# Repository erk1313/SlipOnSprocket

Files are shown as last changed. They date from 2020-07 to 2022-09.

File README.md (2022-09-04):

### Slip-On Sprocket for the Early-Rider 16" Belt-Driven Bicycle

The Early Rider Belter/Seeker 16 comes with a tall gear ratio that's tough for hilly areas or timid riders.  The easiest thing is to buy a bike with a chain with a replaceable sprocket, but what's the fun in that?! This project is for a rear sprocket that slips over the existing 22t sprocket.

Here's how the gain ratio of popular 16" bikes stack up.  Lower ratios make it easier to climb hills, while higher ratios limit top speed on straight-aways.  The Early Rider comes with a 46t front chainring and a 22t rear sprocket, making it the highest gain ratio on this list

### Gain Ratios of 16" bikes*
| Bike | Gain Ratio | Gear Ratio  | Crank Length  | TIRE OD | Notes|
|---|---|---|---|---|---|
|Early Rider (Seeker)|4.05 |46/22t **STOCK**|105mm |407mm**  ||
|Spawn Yoji |3.97 |24/12t |102mm |405mm* | |
|Prevalo Alpha |3.80 |25t/14t |**95mm** |403mm* |Gain Ratio listed on [Prevalo](https://prevelobikes.com/products/alpha-two) |
|Early Rider (Hellion)|3.70 |30/15t |110mm |407mm**  || 
|Woom 3 |3.54 |25/15t | **95mm** |403mm* ||
|Islabike Cnoc |3.52 |25/14t |102mm |401mm* ||
|Priority Start |3.38 |? |? |? |Gain Ratio listed on [Priority Start](https://www.prioritybicycles.com/products/startfw2) |
|Commencal Ramones |3.12 |28/16t |114mm |407mm**  ||
|Cleary Hedgehog |3.09 |25/16t |102mm |404mm* |Flip-flop hub with 14t would result in Gain Ration of 3.54 (like a Woom 3)|
|Early Rider (Seeker)|2.97 |46/30t **CUSTOM**|105mm |407mm**  ||
|Early Rider (Seeker)|2.79 |46/32t **CUSTOM**|105mm |407mm**  ||

(*) *Tire OD estimated based on tire width (not very accurate)*

(**) *Tire OD measured by marking one circumference, then dividing by pi.  YMMV...If you own one of these bikes, please measure and update the tire diameter :)*

> *Gain ratio?* You mean gear ratio?  
[Gain ratio](https://prevelobikes.com/blogs/news/bicycle-gear-ratio-gear-inches-and-gain-ratio) takes into account the size of the tires and the crank length, which factor in to how easy it is to pedal. Thanks Prevalo, for your awesome [Gain Ratio Calculator] (https://prevelobikes.com/blogs/news/gear-ratio-gear-inches-gain-ratio-calculator).

### Early Rider - Stock Specs
Here are the specs that determine the gain ratio on the stock bike:
* Front Chainring: 46t
* Rear Sprocket: 22t
* Crank: 105mm
* Tire Diameter: 406.8mm (Vee-Crown Gem 16" x 2.25" width).  
Plugging that in the gain ratio calculator yields 4.05.  Suprisingly, the Spawn Yoji is also high on the list, even though it is meant for the bike park.  

### Lowering the Gain Ratio with a New Rear Sprocket
With a belt drive, you can't just add a link in the chain to make it longer. The stock belt is a 840mm long and the next size up is 880mm long.
>Stock belt: Gates HTD series, which is a round tooth profile.  840-8M-12 translates to 880mm long; 8mm pitch (spacing between teeth); 12mm width
 
If we want to keep the distance between the front and rear axles the same, then the belt length is going to dictate the number of rear teeth (assuming the front chainring stays the same).  With the new belt length of 880mm, the rear sprocket needs to be 32t.  We could cheat it a bit, by allowing the rear axle to slip back.

|Gear Ratio |Belt Length  |Axle Spacing*  |Change in Spacing from Stock|
|---|---|---|---|
|Stock 46/22t |840mm |282mm (11.11in)| |
|46/32t |880mm |283mm (11.16in)|+0.05 |
|46/31t |880mm |285mm (11.23in)|+0.12 |  
|46/30t |880mm |287mm (11.31in)|+0.20 | 
* *Axle spacing is based on the theoretical pitch diameter.  It seems that Early Rider varied from this, which would have effected the actual axle spacing.

>Solidworks figures all this out for me... Here is an image of the stock setup.


With the 32t slip-on sprocket and a newly tensioned belt, I had to move the rear wheel back about 1/16" (as expected).  This is great if you can live with the really low gain ratio.  For now, it works beautifully for my son.  He can now climb hills to get around all by himself.

With the 32t setup, I have about 0.18" more travel in the horizontal dropout.  So one might be able to accomodate the 30t or 31t sprocket. it would require repositioning the rear brake pads, which are also near their limit.  If we get some interest in another order, I can try to mock up what the brakes would look like with the rear wheel shifted.

### Photo Gallery



[Video of a 4-yr with a 32t Slip-on Sprocket installed](Photos/SlipOn_46-32t.mp4)

### Revision Notes
*Rev-A*: The first run was a batch of 3 parts.  The clearance between the existing sprocket and the matching interior of the slip-on sprocket was 0.005" (radially). This fit perfect!  All three parts were tested on my 2020 Seeker, as well as an old hub I bought off a member, which had a screw on hub instead of the current spline. I was actually surprised.  YMMV as I used a cheap Chinese fabricator with no specified tolerance on machining (to keep cost down).  They inner face was also bead blasted, which could have helped.  If needed, the design might fit more universally with a 0.007"-0.010" clearance and making up the slop with a expandable pin. 

*Rev-1.0* (unreleased - see Develop branch): Changed clearance for the internal teeth from 0.005" to 0.010" for better fit.  Added tappd set screw (10-32 x .375") to retain the sprocket.

Note: The sprocket requires a longer belt, but is cheap and standard.  HTD 880-8M-12
- https://www.3bgsupply.com/880-8m-12-d-d-global $9

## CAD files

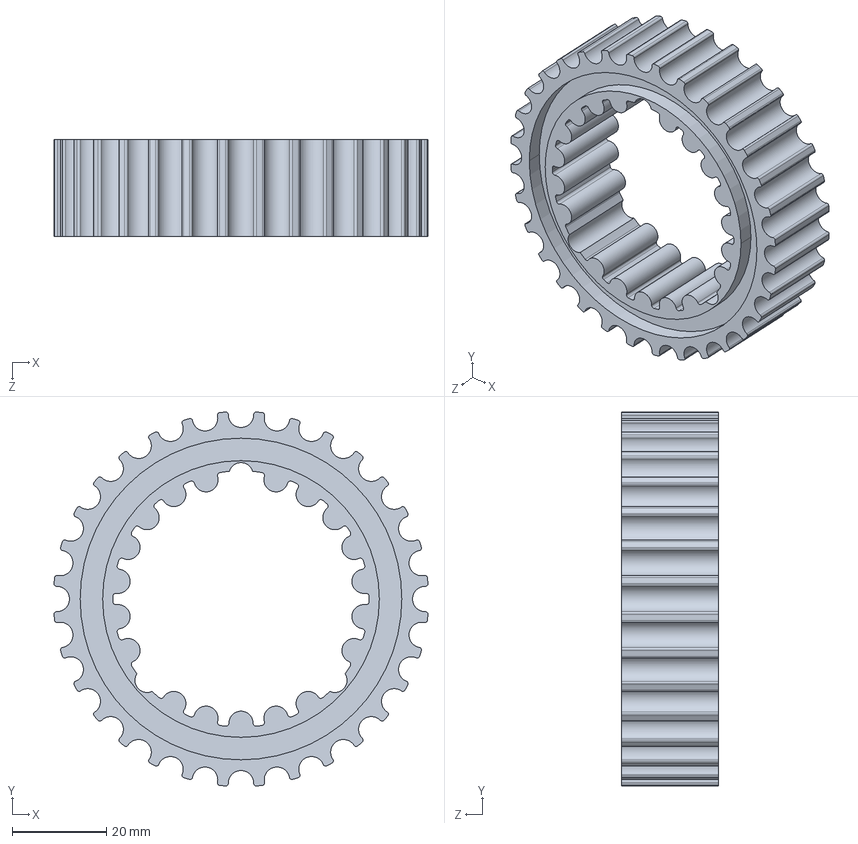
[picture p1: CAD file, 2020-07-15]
CAD/SlipOnSprocket_32t_Rev-A.STEP
79.3 x 79.3 x 20.6 mm

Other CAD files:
CAD/BeltLengthCalc.SLDPRT
CAD/SlipOnSprocket_32t.SLDDRW
CAD/SlipOnSprocket_32t_Rev-A.SLDPRT
CAD/SlipOnSprocket_32t_Rev-A.STL

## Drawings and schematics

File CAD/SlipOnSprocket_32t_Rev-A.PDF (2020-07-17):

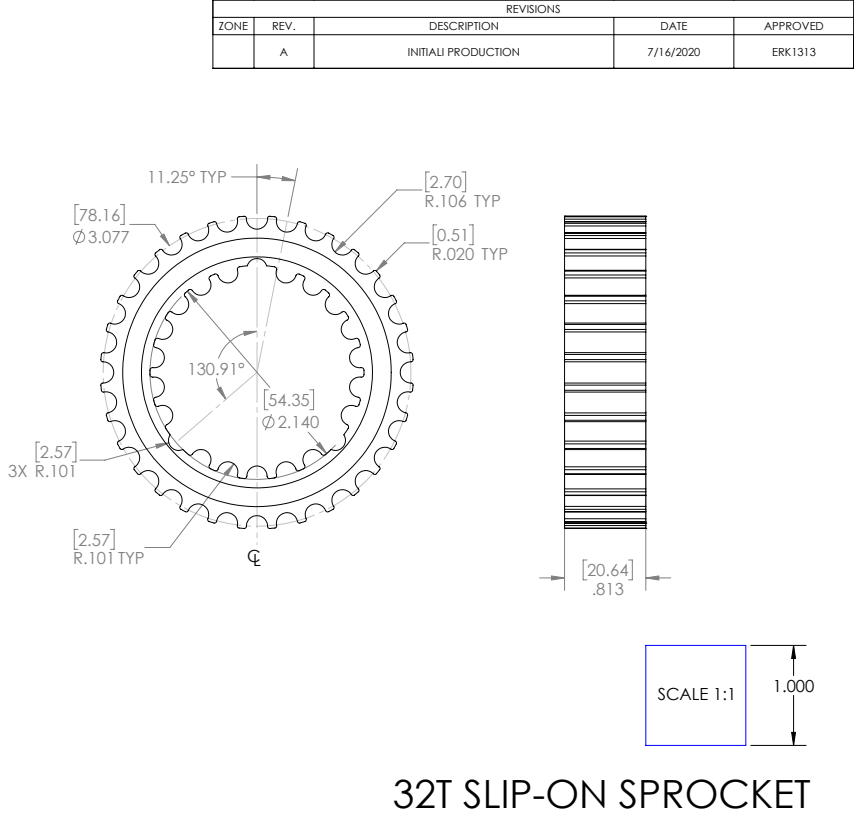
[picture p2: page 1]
R.106 TYP; R.020 TYP; R.101 TYP; 11.25° TYP; SCALE 1:1

ZONE | REV. | DESCRIPTION | DATE | APPROVED

A | INITIALI PRODUCTION | 7/16/2020 | ERK1313

32T SLIP-ON SPROCKET

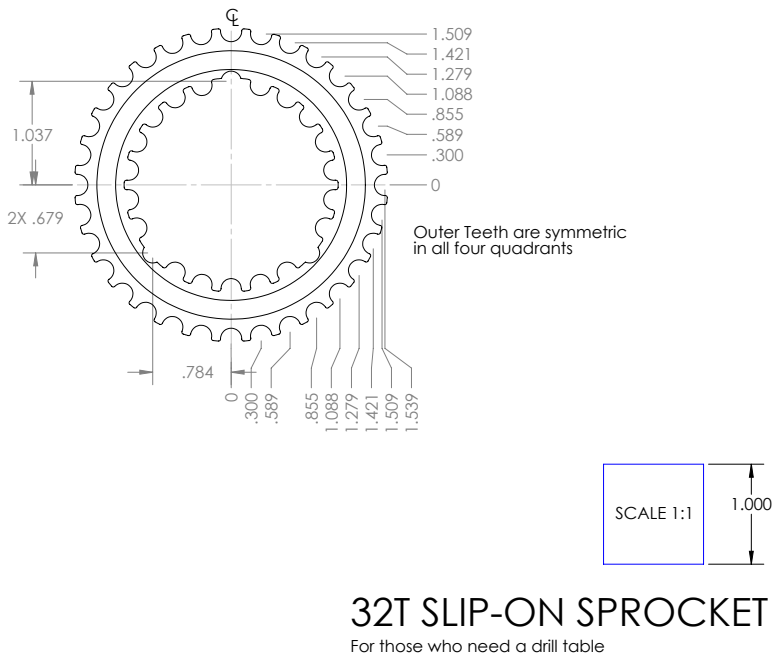
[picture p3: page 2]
SCALE 1:1

Outer Teeth are symmetric
in all four quadrants

32T SLIP-ON SPROCKET

For those who need a drill table

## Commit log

2020-07-15 Uploaded CAD and Video
    Uploaded CAD and Video
    [BeltLengthCalc.SLDPRT, SlipOnSprocket_32t_Rev-A.SLDPRT, SlipOnSprocket_32t_Rev-A.STEP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]
2020-07-17 Added drawing.
    Note that internal clearance to existing sprocket is 0.005" (radially). Drawing tolerances are generic and don't represent true tolerances.
